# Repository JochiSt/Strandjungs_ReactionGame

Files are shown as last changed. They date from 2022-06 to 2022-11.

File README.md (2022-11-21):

# Reaction Game

The idea of this game is that you press a button and after some time (random)
one or two (selectable) wooden rods are dropped. The player has to catch these 
falling rods.

## Modes

There are four different modes implemented. The selection of the modes is done 
via the binary encoded input from the switch (marked with Drop 1/2).
Switch 1 is the LSB and two the MSB.

| Switch 2 	| Switch 1 	| Mode 	| Action 	|
|---	|---	|---	|---	|
| 0 	| 0 	| 0 	| dropping a single random rod 	|
| 0 	| 1 	| 1 	| dropping two random rods at the same time 	|
| 1 	| 0 	| 2 	| dropping two random rods at different times 	|
| 1 	| 1 	| 3 	| dropping all rods after each other (with waiting time) in a random order 	|

## Operation Voltage & Current
The operation voltage is 12V and the power consumption is about 1.5A (5x200mA for the magnets). 

## Hardware used
* [ElectroMagnets](https://www.amazon.de/gp/product/B07QNL3CJ2)

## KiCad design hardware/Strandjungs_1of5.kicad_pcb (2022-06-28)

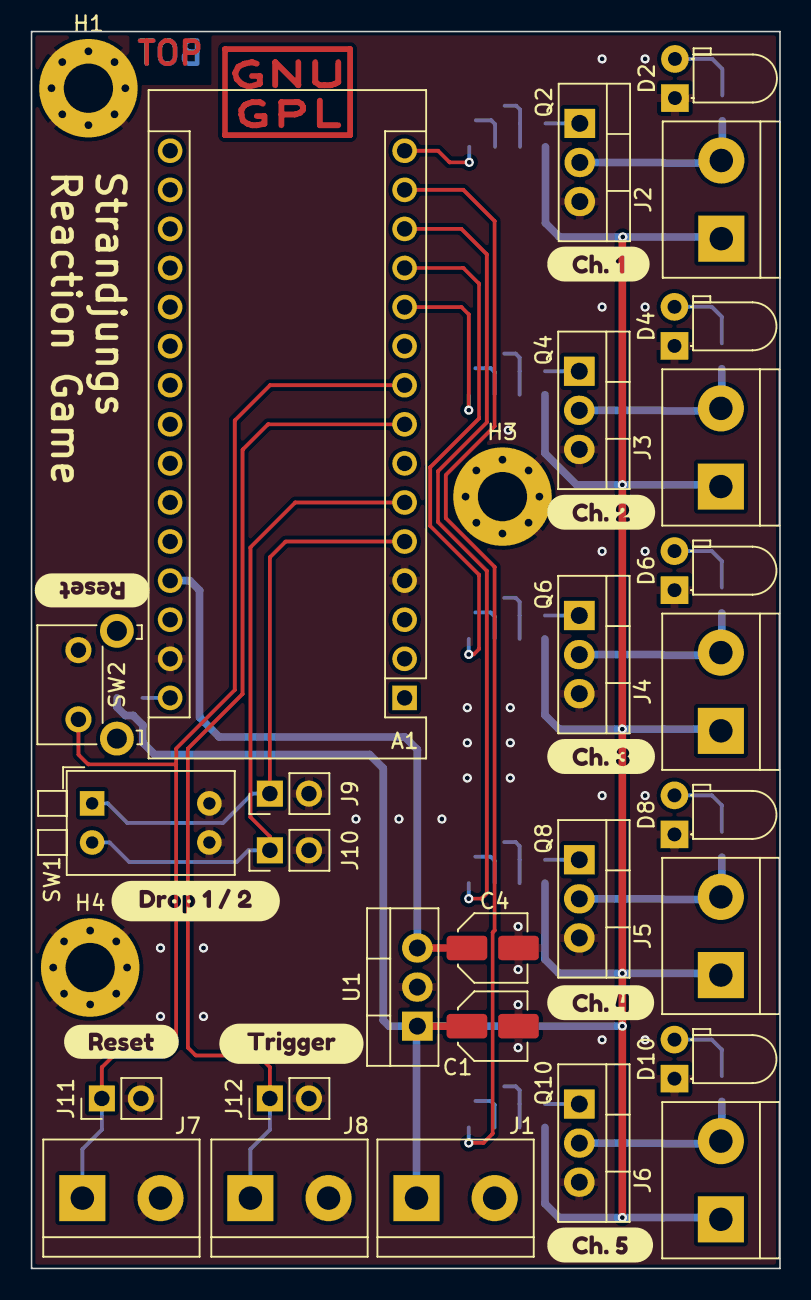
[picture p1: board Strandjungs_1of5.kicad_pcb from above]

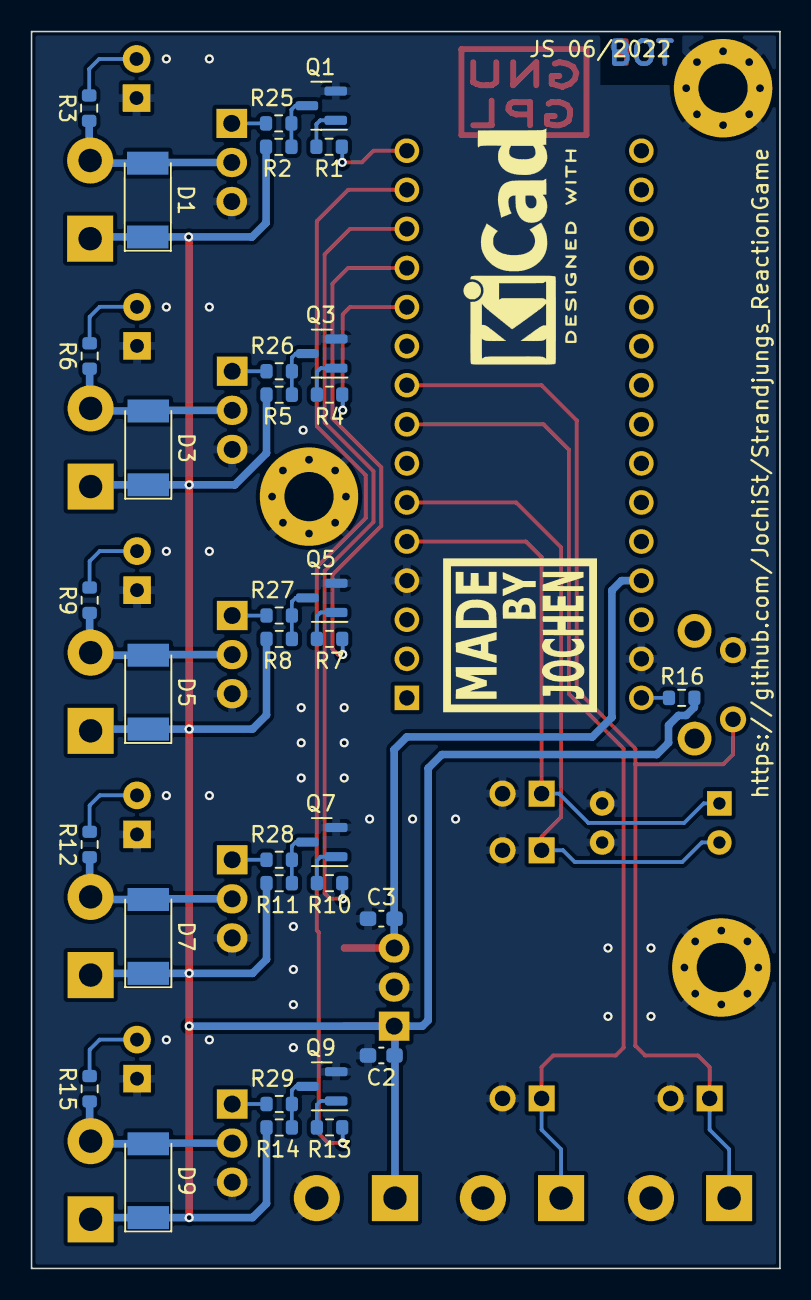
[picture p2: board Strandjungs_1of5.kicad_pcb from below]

Board: 2 copper layers, 48.6 x 80.4 mm, 73 parts (33 on the bottom side), 38 nets.

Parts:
A1: Arduino_Nano_v2.x; Arduino_Nano
C1: 1uF; C_Elec_4x5.4
C2, C3: 100n; C_0603_1608Metric_Pad1.08x0.95mm_HandSolder
C4: 10uF; C_Elec_4x5.4
D1, D3, D5, D7, D9: SM4001; D_MELF
D2, D4, D6, D8, D10: LED; LED_D3.0mm_Horizontal_O1.27mm_Z2.0mm
H1, H3, H4: MountingHole_Pad; MountingHole_3.2mm_M3_Pad_Via
J1, J2, J3, J4, J5, J6, J7, J8: Screw_Terminal_01x02; TerminalBlock_bornier-2_P5.08mm
J9, J10, J11, J12: Conn_01x02; PinHeader_1x02_P2.54mm_Vertical
Q1, Q3, Q5, Q7, Q9: BC847; SOT-23
Q2, Q4, Q6, Q8, Q10: BUZ11; TO-220-3_Vertical
R1, R2, R4, R5, R7, R8, R10, R11, R13, R14: 10k; R_0603_1608Metric
R3, R6, R9, R12, R15: 5k6; R_0603_1608Metric
R16: dnp; R_0603_1608Metric
R25, R26, R27, R28, R29: 56; R_0603_1608Metric
SW1: SW_DIP_x02; SW_DIP_SPSTx02_Piano_10.8x6.64mm_W7.62mm_P2.54mm
SW2: SW_Push; SW_Tactile_SKHH_Angled
U1: L7805; TO-220-3_Vertical
kibuzzard-62B9DC86: G***; kibuzzard-62B9DC86
kibuzzard-62B9DCAD, kibuzzard-62B9DCAD#2: G***; kibuzzard-62B9DCAD
kibuzzard-62B9DCC5: G***; kibuzzard-62B9DCC5
kibuzzard-62B9DCD6: G***; kibuzzard-62B9DCD6
kibuzzard-62B9DCE2: G***; kibuzzard-62B9DCE2
kibuzzard-62B9DCF0: G***; kibuzzard-62B9DCF0
kibuzzard-62B9DD05: G***; kibuzzard-62B9DD05
kibuzzard-62B9DD70: G***; kibuzzard-62B9DD70

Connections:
+5V: A1.27 (+5V), C3.1, C4.1, U1.3 (OUT)
+12V: C1.1, C2.1, D1.1 (K), D3.1 (K), D5.1 (K), D7.1 (K), D9.1 (K), J1.1, J2.1, J3.1, J4.1, J5.1, J6.1, R2.1, R5.1, R8.1, R11.1, R14.1, R16.1, U1.1 (IN)
/Channel 0/MAG_RTN: D1.2 (A), J2.2, Q2.2 (D), R3.1
/Channel 1/MAG_RTN: D3.2 (A), J3.2, Q4.2 (D), R6.1
/Channel 2/MAG_RTN: D5.2 (A), J4.2, Q6.2 (D), R9.1
/Channel 3/MAG_RTN: D7.2 (A), J5.2, Q8.2 (D), R12.1
/Channel 4/MAG_RTN: D9.2 (A), J6.2, Q10.2 (D), R15.1
/RESET: A1.9 (D6), J7.1, J11.1, SW2.1
/SEL_0: A1.5 (D2), J9.1, SW1.1
/SEL_1: A1.6 (D3), J10.1, SW1.2
/SWITCH0: A1.15 (D12), R1.1
/SWITCH1: A1.11 (D8), R4.1
/SWITCH2: A1.12 (D9), R7.1
/SWITCH3: A1.13 (D10), R10.1
/SWITCH4: A1.14 (D11), R13.1
/TRIGGER: A1.8 (D5), J8.1, J12.1
GND: A1.4 (GND), A1.29 (GND), C1.2, C2.2, C3.2, C4.2, D2.1 (K), D4.1 (K), D6.1 (K), D8.1 (K), D10.1 (K), H1.1, H3.1, H4.1, J1.2, J7.2, J8.2, J9.2, J10.2, J11.2, J12.2, Q1.2 (E), Q2.3 (S), Q3.2 (E), Q4.3 (S), Q5.2 (E), Q6.3 (S), Q7.2 (E), Q8.3 (S), Q9.2 (E), Q10.3 (S), SW1.3, SW1.4, SW2.2, U1.2 (GND)
unnamed: A1.30 (VIN), R16.2
unnamed: D2.2 (A), R3.2
unnamed: D4.2 (A), R6.2
unnamed: D6.2 (A), R9.2
unnamed: D8.2 (A), R12.2
unnamed: D10.2 (A), R15.2
unnamed: Q1.1 (B), R1.2
unnamed: Q1.3 (C), R2.2, R25.1
unnamed: Q2.1 (G), R25.2
unnamed: Q3.1 (B), R4.2
unnamed: Q3.3 (C), R5.2, R26.1
unnamed: Q4.1 (G), R26.2
unnamed: Q5.1 (B), R7.2
unnamed: Q5.3 (C), R8.2, R27.1
unnamed: Q6.1 (G), R27.2
unnamed: Q7.1 (B), R10.2
unnamed: Q7.3 (C), R11.2, R28.1
unnamed: Q8.1 (G), R28.2
unnamed: Q9.1 (B), R13.2
unnamed: Q9.3 (C), R14.2, R29.1
unnamed: Q10.1 (G), R29.2

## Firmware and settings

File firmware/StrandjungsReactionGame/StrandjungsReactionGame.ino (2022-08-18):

/**
   Strandjungs Reaction Game

   Hardware Arduino Nano

   Select Board:
      "Arduino Nano"
   Prozessor:
      "ATmega328P (Old Bootloader)"
   Port:
      the Port, which the Arduino is connected to

   Mode:
    A - Drop single wood
    B - Drop two woods at the same time
    C - Drop two woods each at their individual time
    D - Drop all rods after each other with their individual time

   If trigger button is pressed, wait 2 to 10 seconds, then release a wooden rod, which should be catched by the player.
*/

// define all buttons
#define BTN_TRG     5 // trigger button
#define BTN_RST     6 // reset button
#define SEL_MODE_1  2 // mode selection 1
#define SEL_MODE_2  3 // mode selection 2

#define BOARD_LED   13 // on board LED

#define COIL_ON   LOW
#define COIL_OFF  HIGH

enum DROP_MODE {
                    //      switch positions
  SINGLE_ROD,       // 0 => 00
  DUAL_ROD,         // 1 => 01
  DUAL_ROD_TIME,    // 2 => 10
  ALL_ROD_TIME      // 3 => 11
};

// array of the magnet outputs
int magnets[5] = {8, 9, 10, 11, 12};

void setup() {
  // put your setup code here, to run once:
  randomSeed(analogRead(A0));
    
  // outputs to 5 electro magnets
  for(int i=0; i<5; i++){
    pinMode( magnets[i], OUTPUT );
    digitalWrite( magnets[i], COIL_OFF);
  }

  pinMode(BOARD_LED, OUTPUT);

  // trigger button input
  pinMode( BTN_TRG, INPUT_PULLUP );

  // reset button
  pinMode( BTN_RST, INPUT_PULLUP );

  // mode selection inputs
  pinMode( SEL_MODE_1, INPUT_PULLUP );
  pinMode( SEL_MODE_2, INPUT_PULLUP );

  Serial.begin(115200);
  Serial.print("Strandjungs reaction game initialised...\n");

  for(int i=0; i<5; i++){
    Serial.print("Testing channel: ");
    Serial.print(i);
    Serial.print("\n");
    digitalWrite(BOARD_LED, COIL_ON);
    digitalWrite(magnets[i], COIL_ON);
    delay(1000);
    digitalWrite(BOARD_LED, COIL_OFF);
    digitalWrite(magnets[i], COIL_OFF);
  }

  digitalWrite(BOARD_LED, true);
}

// function to define the waiting time for the rods
void wait_rod(){
  float timewait = random(0, 400);  // wait between 0 and 800 (unit 10ms)
  timewait = (timewait*10) + 1000;
  Serial.print("Waiting for: ");
  Serial.print( timewait );
  Serial.print("ms \n");
  delay( timewait);   // unit ms
}

void loop() {
  Serial.print("waiting for button\n");
  digitalWrite(BOARD_LED, false);
  
  ///////////////////////////////////////////////////////
  // wait until button is pressed
  bool trigger_state = digitalRead(BTN_TRG);
  while(trigger_state == digitalRead(BTN_TRG)){
    delay(10);
  }
  // button is triggered
  // if button is pressed dice rod and wait random time
  digitalWrite(BOARD_LED, true);
  Serial.print("Button pressed\n");
  ///////////////////////////////////////////////////////
  // check mode pins
  bool sel_0 = digitalRead(SEL_MODE_1);
  bool sel_1 = digitalRead(SEL_MODE_2);

  DROP_MODE mode = sel_1 << 1 | sel_0;
  Serial.print("Mode: ");
  Serial.print(mode);
  Serial.print("\n");

  // random(start, end) - inclusive start, exclusive end
  int rod1 = random(0, 5);          // dice the rod, which should be dropped
  int rod2 = random(0, 5);
  // ensure, that both rods are different
  while(rod1 == rod2){
    rod2 = random(0, 5); 
  }

  ///////////////////////////////////////////////////////
  // wait
  wait_rod();

  ///////////////////////////////////////////////////////
  // drop the rods according to the mode selection
  if(mode == SINGLE_ROD || mode == DUAL_ROD || mode == DUAL_ROD_TIME){
    Serial.print("Dropping Rod: ");
    Serial.print(rod1);
    Serial.print("\n");
    digitalWrite(magnets[rod1], COIL_OFF);
  }
  // drop two rods at the same time
  if(mode == DUAL_ROD){
    Serial.print("Dropping Rod: ");
    Serial.print(rod2);
    Serial.print("\n");
    digitalWrite(magnets[rod2], COIL_OFF);
  }

  // some additional modes, which are more or less experimental
  // drop two rods after each other
  if(mode == DUAL_ROD_TIME){
    wait_rod();
    Serial.print("Dropping Rod: ");
    Serial.print(rod2);
    Serial.print("\n");
    digitalWrite(magnets[rod2], COIL_OFF);
  }

  // drop all rods after each other
  if(mode == ALL_ROD_TIME){
    bool dropped_rods[5] = {false, false, false, false, false};
    for(int i=0; i<5; i++){
      int rod = random(0, 5);
      while( dropped_rods[rod] ){
        rod = random(0, 5);
      }
      // we have found a rod, which is not yet dropped
      // drop rod
      Serial.print("Dropping Rod: ");
      Serial.print(rod);
      Serial.print("\n");
      digitalWrite(magnets[rod], COIL_OFF);
      // mark rod as dropped
      dropped_rods[rod] = true;
      
      if(i < 4){
        // wait for all rods, but not for the last one
        wait_rod();
      }
    }
  }
  
  delay(1000);  // wait for the rod(s) to fall down
  
  // set all rods to be active again
  for(int i=0; i<5; i++){
    digitalWrite( magnets[i], COIL_ON);
  }
  Serial.print("ready for next try\n");
}

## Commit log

2022-06-27 added hardware layout
    started layout for driver PCB
    [Strandjungs_1of5.kicad_pcb, Strandjungs_1of5.kicad_sch, switch_channel.kicad_sch]
2022-06-27 first iteration of layout almost done
    [Strandjungs_1of5.kicad_pcb, Strandjungs_1of5.kicad_sch, switch_channel.kicad_sch]
2022-06-27 added 7805 as voltage regulator
    [Strandjungs_1of5.kicad_pcb, Strandjungs_1of5.kicad_sch, switch_channel.kicad_sch]
2022-06-28 updated layout
    [Strandjungs_1of5.kicad_pcb, Strandjungs_1of5.kicad_sch]
2022-06-28 added description of function
    [switch_channel.kicad_sch]
2022-06-28 updated AISLER project ID
    [Strandjungs_1of5.kicad_pcb]
2022-06-28 adjusted production output
    [Strandjungs_1of5.kicad_pcb]
2022-06-29 added pins from schematic
2022-07-03 added rough programming scheme
    some action implemented, needs refinement, once the PCB arrives
2022-07-12 fixed polarity of the system
    [StrandjungsReactionGame.ino]
2022-07-13 set random seed
    no longer always having the same pattern of dropped rods
    [StrandjungsReactionGame.ino]
2022-07-29 moved waiting into function
    by this the waiting time for all rod dropping actions is always the same (randomized)
2022-07-29 moved button press action to the very beginning
    by this it is no longer required to have one drop in the old mode, when the mode switches are changed.
    [StrandjungsReactionGame.ino]
2022-07-29 fixed dual rod time mode
    [StrandjungsReactionGame.ino]
2022-08-18 added switch position description
2022-11-21 added link to used magnets
2022-11-21 added operation voltage & current estimate
